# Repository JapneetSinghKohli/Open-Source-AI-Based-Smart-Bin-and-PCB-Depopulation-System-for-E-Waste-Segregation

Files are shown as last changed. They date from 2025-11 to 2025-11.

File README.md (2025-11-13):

# Open-Source-AI-Based-Smart-Bin-and-PCB-Depopulation-System-for-E-Waste-Segregation
Open-source project combining an AI-based smart bin for simple e-waste sorting with a basic PCB depopulation system. Uses computer vision to detect and classify items, separate components, and support small-scale recycling. Includes starter hardware, control code, and easy-to-use AI models.

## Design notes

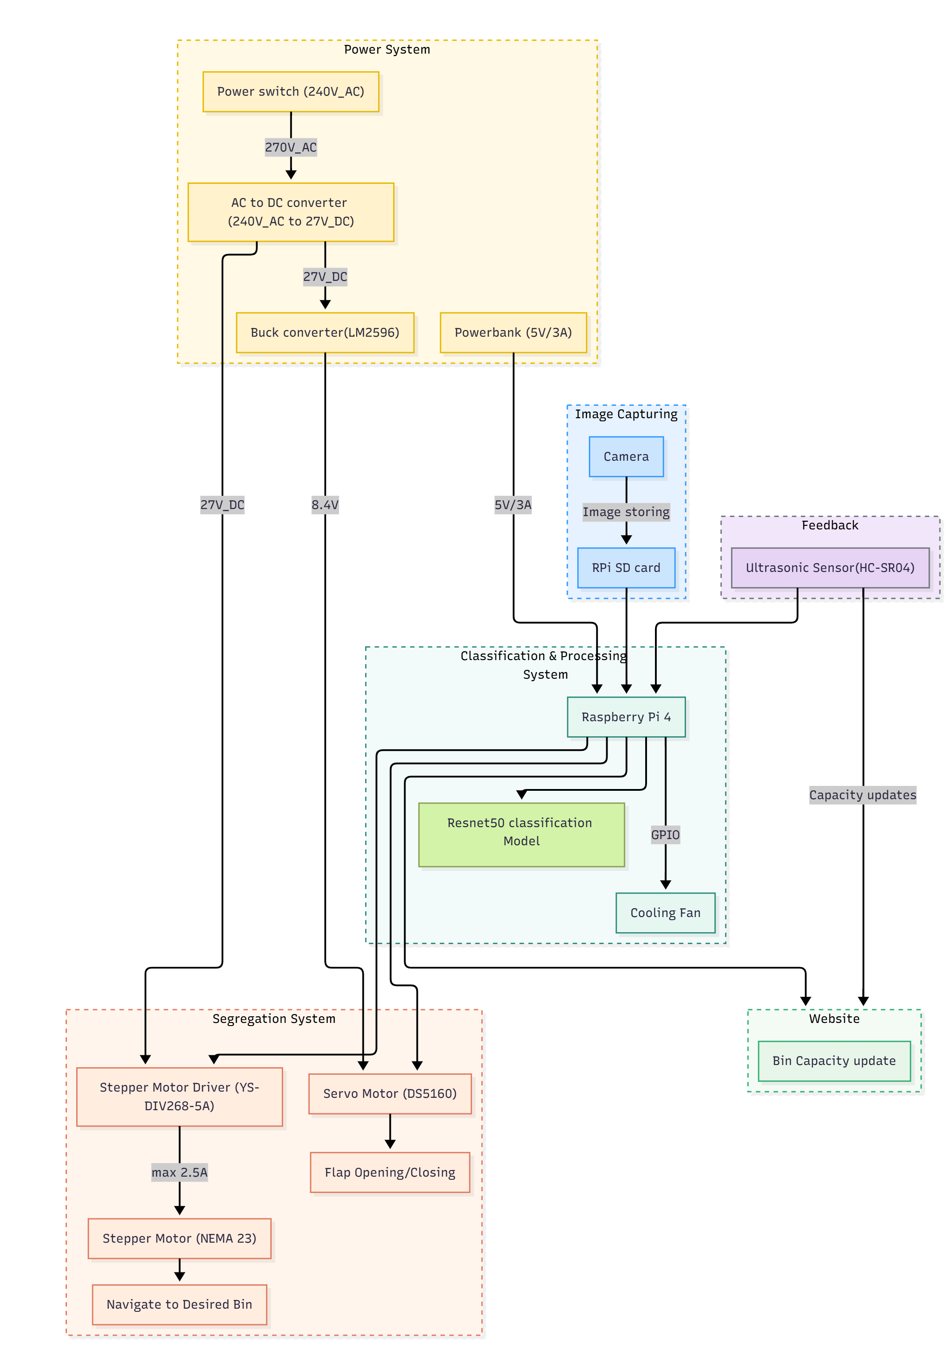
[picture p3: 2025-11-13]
Electronics design and Software/Bin-Cuircuit-Chart.png

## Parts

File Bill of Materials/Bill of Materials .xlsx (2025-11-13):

Total Spending | 48463
Part Name | Assembly Name | Type | Manufacturing Method | Assembly Method | Purchased | CAD Design Status | Reason, if CAD Not Required | Price | Quantity | Invoice Number | Bills | Date of Purchase | Vendor | Reason, if Others was choosen in any of the options
Mild Steel | Metal Frame | Raw Material for Manufacturing | Other | Welding | Offline | CAD Design Complete |  | 2196 |  | #99 | mild steel.pdf (https://drive.google.com/file/d/1QIsmK4YCOdgf_3yenXNvHcopvkcRDPWO/view?usp=sharing) | 2025-09-25 | A2Z
MS Sheet | Metal Frame | Raw Material for Manufacturing |  |  | Offline | CAD Design Complete |  | 2823 |  | #125 | MS Sheet.pdf (https://drive.google.com/file/d/1ynHdcNWmX0iU-SB3GtMpC10SeeWes1UX/view?usp=sharing) | 2025-10-08 | A2Z
Raw Material For Smart Bin | Frame | Raw Material for Manufacturing | Machining (Cutting & Drilling) | Other | Offline | CAD Design Complete |  | 3756 |  | #162 | Bill (https://drive.google.com/file/d/1nSvVK4zmFAYykZs3HyDOkAmtJ0UntyIS/view?usp=sharing) | 2025-10-14 | A2Z
Acrylic ,Paint and GI Sheet | PCB Depopulator Assembly | Raw Material for Manufacturing | Sheet Forming | Other | Offline | CAD Design Complete |  | 6469 |  | #228 | a2z bill paint acrylic and more.pdf (https://drive.google.com/file/d/1YQiOJzQaHguRpVuHmRqeH_DYfBSCvXcD/view?usp=sharing) | 2025-11-01 | A2Z
GI Sheet | Bin Structure | Raw Material for Manufacturing | Machining (Cutting & Drilling) | Other | Offline | CAD Design Complete |  | 2242 | 5 | #110 | GI sheet.pdf (https://drive.google.com/file/d/1pPkF1sUb3jVbSXK8Jkx9vuyRyn9DvjNU/view?usp=sharing) | 2025-09-30 | A2Z
MS + acrylic sheet | Covering and stand for PCB | Raw Material for Manufacturing |  |  | Offline |  |  | 9236 |  | #263 | ms+acrylic for covering .pdf (https://drive.google.com/file/d/1w8mb9un_-gyej0ABCXyPSvSI_XO86tZ7/view?usp=sharing) | 2025-11-05 | A2Z
Screws Nut Bolts | Metal Frame and Bin Structure | Fastnerm | 3D Printing | Fastening | Borrowed from DP Lab | CAD Not Required | Screws already available in Solidworks | 125 |  | #2676 | bill screw.pdf (https://drive.google.com/file/d/1irVYZd-OhjhZvoA9C_F9mrRy1DQCUNAO/view?usp=sharing) | 2025-10-10 | Ram Traders
Ultrasonic Sensor | Electrical Circuit | Purchased Finished Part | Purchased Directly | Fastening | Offline | CAD Design Complete | Electrical Component | 500 | 5 | 339/2025-26 | IMG20251017220716.heic (https://drive.google.com/file/d/1f3cun6vM0CME-H2_nhXB5eU8_ZWsTGwJ/view?usp=sharing) | 2025-10-17 | Audio Video Service Centre
WebCam | Electrical Circuit | Purchased Finished Part | Purchased Directly | Other | Online | CAD Not Required | Electrical Component | 669 | 1 | DED4-2595154 | invoice (1).pdf (https://drive.google.com/file/d/1WdGgs8KD7S56VyLepoplHJlvFNQ7aw7m/view?usp=sharing) | 2025-10-16 | Amazon
WebCam Marketplace fee |  |  |  |  |  |  |  | 5 |  | MKT-257212707 | invoice (1).pdf (https://drive.google.com/file/d/1WdGgs8KD7S56VyLepoplHJlvFNQ7aw7m/view?usp=sharing) | 2025-10-16 | Amazon
Speaker Module | Electrical Circuit | Purchased Finished Part | Purchased Directly | Other | Online | CAD Not Required | Electrical Component | 399 | 1 | ATX1-567154 | speaker bill.pdf (https://drive.google.com/file/d/1GJXc40_ItxIw6FTe9bssWk-4YPDabVqV/view?usp=sharing) | 2025-10-30 | Amazon
Speaker Module Marketplace fee |  |  |  |  |  |  |  | 5 |  | MKT-272847070 | speaker bill.pdf (https://drive.google.com/file/d/1GJXc40_ItxIw6FTe9bssWk-4YPDabVqV/view?usp=sharing) | 2025-10-30 | Amazon
Power Bank | Electrical Circuit | Purchased Finished Part | Purchased Directly | Other | Online | CAD Not Required | Electrical Component | 579 | 1 | DEL5-5873163 | invoice.pdf (https://drive.google.com/file/d/1hK2ikUXvXrY95qX3oZ5XYhJPMcIkzyN7/view?usp=sharing) | 2025-10-04 | Amazon
Power Bank Marketplace fee |  |  |  |  |  |  |  | 5 |  | MKT-224134720 | invoice.pdf (https://drive.google.com/file/d/1hK2ikUXvXrY95qX3oZ5XYhJPMcIkzyN7/view?usp=sharing) | 2025-10-04 | Amazon
Alluminium Heat Sink for Rpi4 | Electrical Circuit | Purchased Finished Part | Purchased Directly | Other | Online | CAD Not Required | Electrical Component | 638 | 1 | #3081509 | WhatsApp Image 2025-11-05 at 00.39.11_f5604e06.jpg (https://drive.google.com/file/d/1APz_-ig_qquVN-FEV0EZqeL5Ppl8Qw_G/view?usp=sharing) | 2025-10-17 | Robu
Case For Rpi4 | Electrical Circuit | Purchased Finished Part | Purchased Directly | Other | Online | CAD Not Required | Electrical Component | 201 | 1 | #3053286 | WhatsApp Image 2025-11-05 at 00.48.45_134bcea7.jpg (https://drive.google.com/file/d/199k05lIHA7o4sRsETyiCau1SaXAZe_My/view?usp=sharing) | 2025-10-04 | Robu
Vacuum Pump | Pump | Purchased Finished Part | Purchased Directly | Other | Offline | CAD Design Complete |  | 2596 | 1 | T1/00420 | vacuum bill.pdf (https://drive.google.com/file/d/1iCdUlG02D-FvGy6mnCbCQ3SVsRM7fInj/view?usp=sharing) | 2025-10-18 | Maini Electricals
Hot Plate | Heating | Purchased Finished Part | Purchased Directly | Other | Online | CAD Design Complete |  | 8024 | 1 | SST/2025-26/008 | hotplate bill.jpg (https://drive.google.com/file/d/11g4U07LEI6_g-2MESX7KZWI6NsFJYkA-/view?usp=sharing) | 2025-10-16 | Sishma Scientific Traders
Fan Blower |  |  |  |  | Online |  |  | 2006 | 1 | 589 | Fan Blower Bill.jpg (https://drive.google.com/file/d/1GNX6yTsFkwgpAt6QHHy39YnqiH1XPK6k/view?usp=sharing) | 2025-10-24 | Mankoo Electric Works
Ceramic Insulation Blanket |  | Purchased Finished Part | Purchased Directly |  | Online | CAD Design Complete |  | 1992 | 1 | IN-568 | Ceramic Blanket.pdf (https://drive.google.com/file/d/103j5b9NfD07mp-TA_c69nZBMUl-d2isc/view?usp=sharing) | 2025-10-28 | Amazon
Ceramic Insulation Blanket Marketplace fee |  |  |  |  |  |  |  | 5 |  | MKT-269632534 | Ceramic Blanket.pdf (https://drive.google.com/file/d/103j5b9NfD07mp-TA_c69nZBMUl-d2isc/view?usp=sharing) | 2025-10-28 | Amazon
Extention Board |  | Raw Material for Manufacturing | Other | Other | Offline | CAD Not Required |  | 1060 | 1 | 3835 | Extension Board Bill.jpg (https://drive.google.com/file/d/1-SyfV-J8QsLSe0toX0ElAZfBRrLgyiDw/view?usp=sharing) | 2025-10-25 | Jiwan Electric Stores
Motor Driver DRV8825 |  | Purchased Finished Part | Purchased Directly |  | Offline |  | Electrical Component | 120 | 1 | 338/2025-26 | IMG20251017220633.heic (https://drive.google.com/file/d/1wcqMyeiRGANEz7x_3AZ8HlOxYGn_FrIG/view?usp=sharing) | 2025-10-17 | Audio Video Service Centre
Load Cell + HX711 |  | Purchased Finished Part | Purchased Directly |  | Offline |  | Electrical Component | 240 | 1+1 | 340/2025-26 | IMG20251017220651.heic (https://drive.google.com/file/d/1sXZ2I21_zPG8-pErcfny125J8XbTL-0H/view?usp=sharing) | 2025-10-17 | Audio Video Service Centre
YS-DIV268-5A Stepper Motor Driver | Electrical Circuit | Purchased Finished Part | Purchased Directly |  | Online |  |  | 1359 | 1 | DEL5-3833545 | motor driver for stepper.pdf (https://drive.google.com/file/d/1ZaReP2N4-LilRE3OmvAkqA1qvz2RBtmh/view?usp=sharing) | 2025-11-01 | Amazon
YS-DIV268-5A Stepper Motor Driver Marketplace fee |  |  |  |  |  |  |  | 5 |  | MKT-276489144 | motor driver for stepper.pdf (https://drive.google.com/file/d/1ZaReP2N4-LilRE3OmvAkqA1qvz2RBtmh/view?usp=sharing) | 2025-11-01 | Amazon
Lab Gloves | Safety | Purchased Finished Part | Purchased Directly |  | Online | CAD Not Required | Safety Component | 399 | 1 | ATX1-723 | gloves.pdf (https://drive.google.com/file/d/1EiizKb7cILWFiQO9119dt_ykNaHlOZkI/view?usp=sharing) | 2025-10-30 | Amazon
Lab Gloves Marketplace fee |  |  |  |  |  |  |  | 5 |  | MKT-273642335 | gloves.pdf (https://drive.google.com/file/d/1EiizKb7cILWFiQO9119dt_ykNaHlOZkI/view?usp=sharing) | 2025-10-30 | Amazon
Power supply | Electrical Circuit | Purchased Finished Part | Purchased Directly |  | Online |  |  | 799 | 1 | RNLH-6357 | power supply bill.pdf (https://drive.google.com/file/d/15PSYE9HjfH0hNEDoG0ndsTIOTZ4xvLA6/view?usp=sharing) | 2025-11-03 | Amazon
Power supply Marketplace fee |  |  |  |  |  |  |  | 5 |  | MKT-280663344 | power supply bill.pdf (https://drive.google.com/file/d/15PSYE9HjfH0hNEDoG0ndsTIOTZ4xvLA6/view?usp=sharing) | 2025-11-03 | Amazon
Battery | Electrical Circuit | Purchased Finished Part | Purchased Directly | Other | Borrowed from DP Lab | CAD Design Complete | Electrical Component | 0 | 1
Servo | Electrical Circuit | Purchased Finished Part | Purchased Directly | Other | Borrowed from DP Lab | CAD Design Complete | Electrical Component | 0 | 2
Stepper Motor | Electrical Circuit | Purchased Finished Part | Purchased Directly | Other | Borrowed from DP Lab | CAD Design Complete |  | 0 | 1
Raspberry Pi | Electrical Circuit | Purchased Finished Part | Purchased Directly | Other | Borrowed from DP Lab | CAD Design Complete | Electrical Component | 0 | 1
Micro Sd card | Electrical Circuit | Purchased Finished Part | Purchased Directly | Other | Borrowed from DP Lab | CAD Design Complete | Electrical Component | 0 | 1
TOTAL |  |  |  |  |  |  |  | 48463

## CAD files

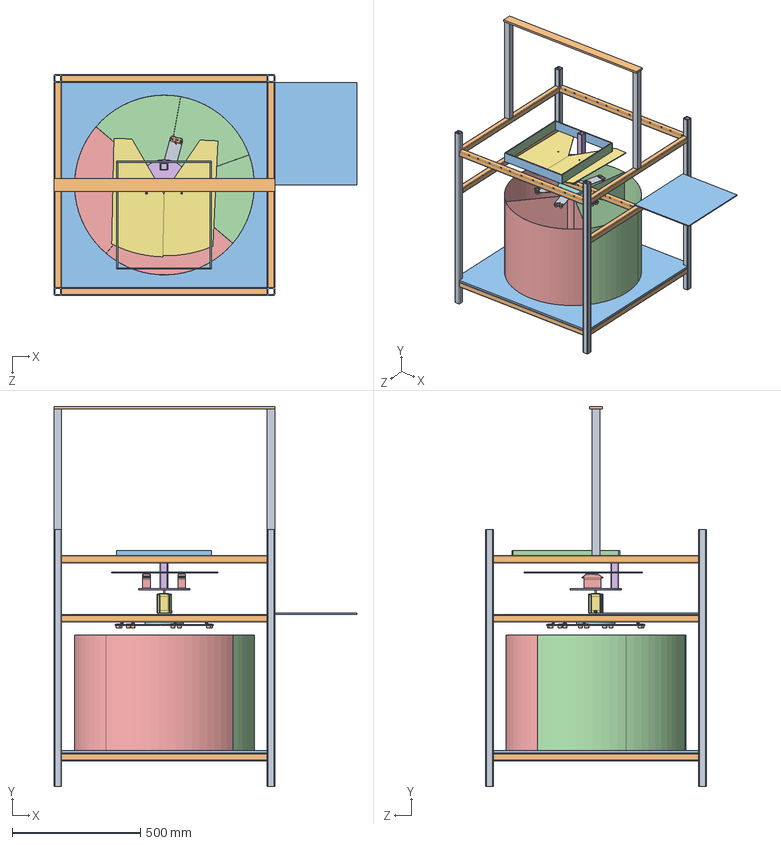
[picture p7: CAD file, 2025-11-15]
CAD/AI Based Smart Bin/Assem1.SLDASM
1180.0 x 1480.0 x 860.0 mm
Bar_2 x 4
bar x 13
sheet
Bin_Compart x 3
Disc
Stepper motor NEMA 23HS7430
mount
bAR1 x 2
camera mount
Wall_1 x 2
wall_2 x 2
ft6560m 60kg.cm.step x 2
wall holder
flaps x 2
UltraHolder
HC-SR04 Ultrasonic Sensor Holder x 5
HCSR04 Ultrasonic Sensor x 5
electronic holder

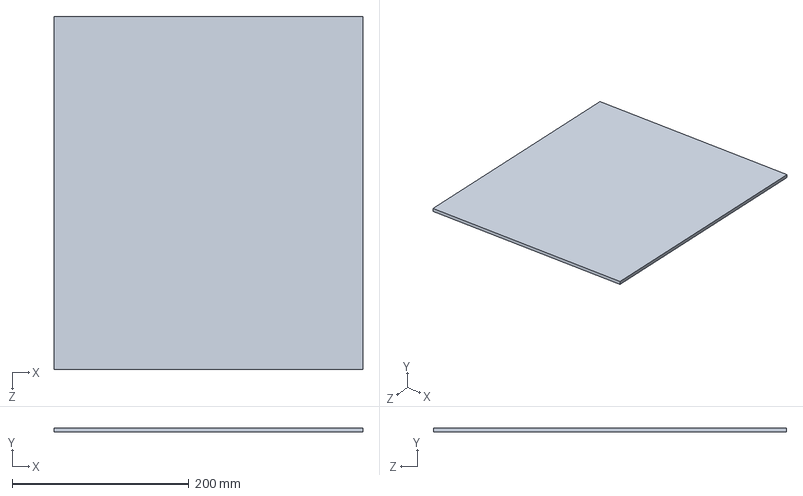
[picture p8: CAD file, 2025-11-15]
CAD/AI Based Smart Bin/electronic holder.SLDPRT
350.0 x 5.00 x 400.0 mm

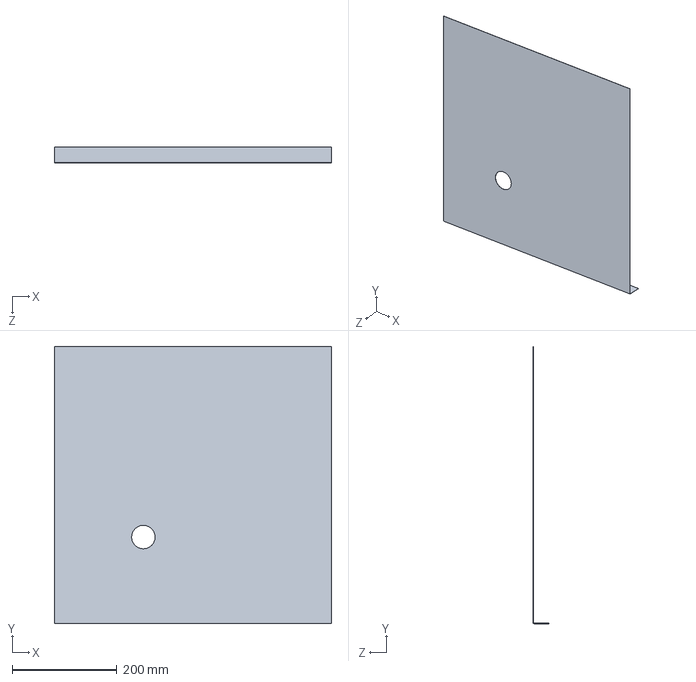
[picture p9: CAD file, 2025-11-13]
CAD/PCB Depopulator/right.SLDPRT
530.0 x 530.0 x 30.4 mm

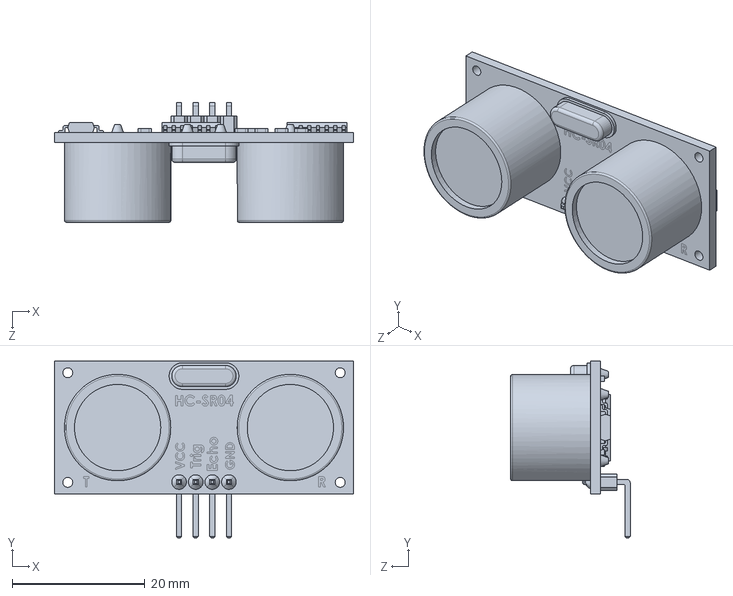
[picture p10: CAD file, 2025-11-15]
CAD/AI Based Smart Bin/HCSR04 Ultrasonic Sensor.SLDPRT
45.0 x 26.6 x 18.0 mm

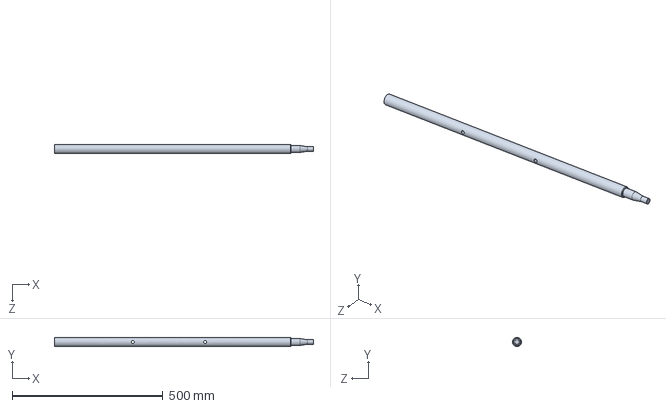
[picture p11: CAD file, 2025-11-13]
CAD/PCB Depopulator/Cylinder.SLDPRT
860.0 x 30.0 x 30.0 mm

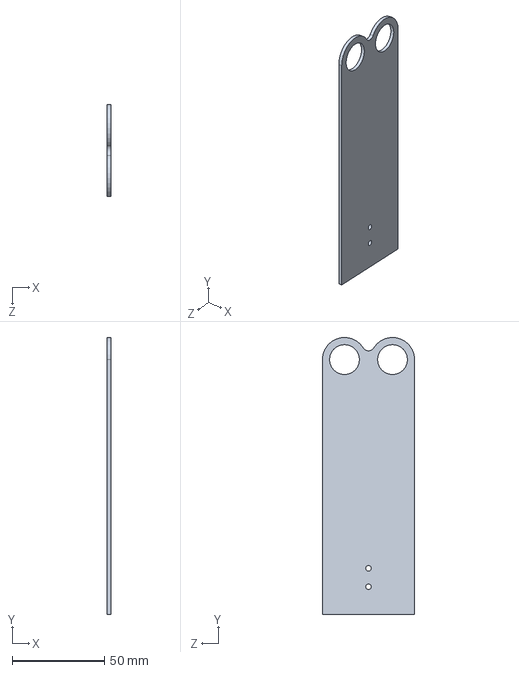
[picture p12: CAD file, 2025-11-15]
CAD/AI Based Smart Bin/HC-SR04 Ultrasonic Sensor Holder.SLDPRT
2.00 x 150.0 x 50.0 mm

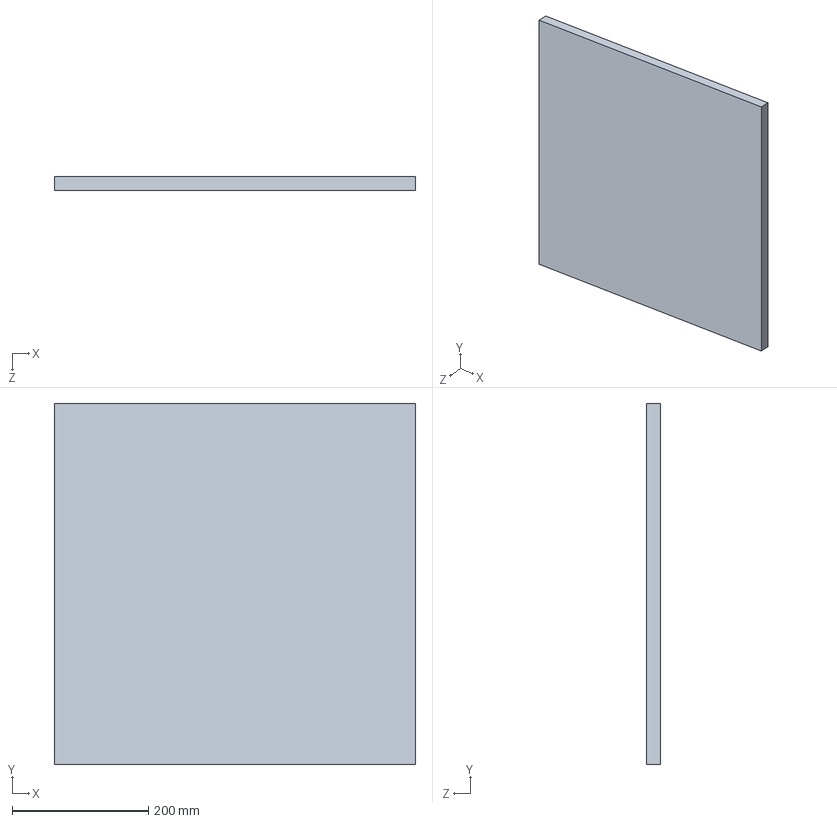
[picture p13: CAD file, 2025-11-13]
CAD/PCB Depopulator/FRONT.SLDPRT
530.0 x 530.0 x 20.0 mm

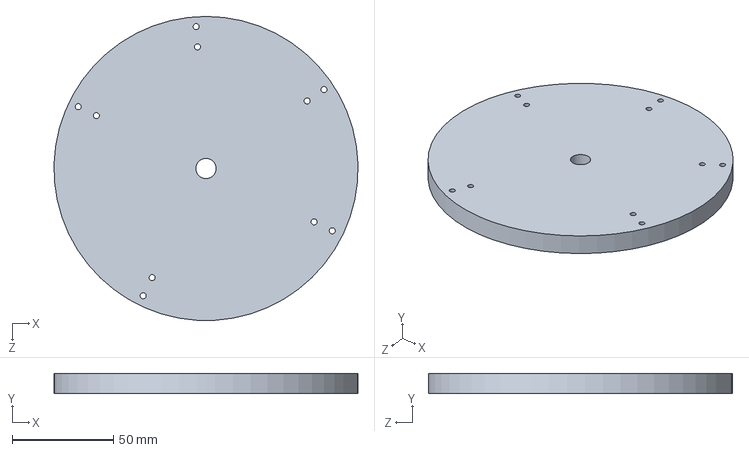
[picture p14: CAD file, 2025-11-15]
CAD/AI Based Smart Bin/UltraHolder.SLDPRT
149.9 x 10.0 x 150.0 mm

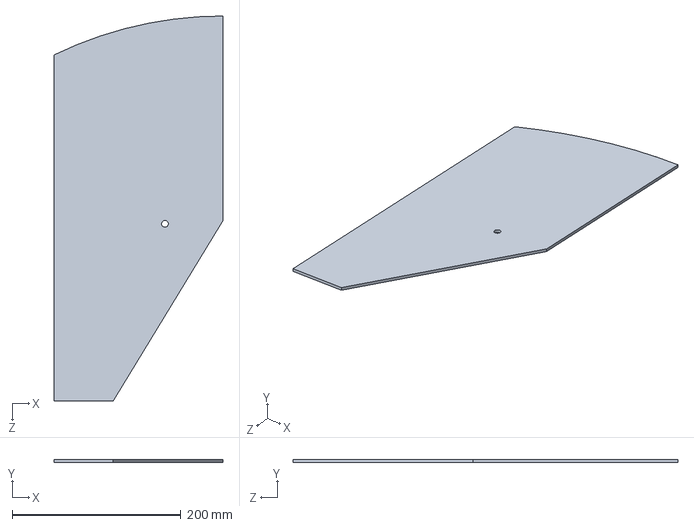
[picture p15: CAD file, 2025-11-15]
CAD/AI Based Smart Bin/flaps.SLDPRT
200.0 x 3.50 x 456.8 mm

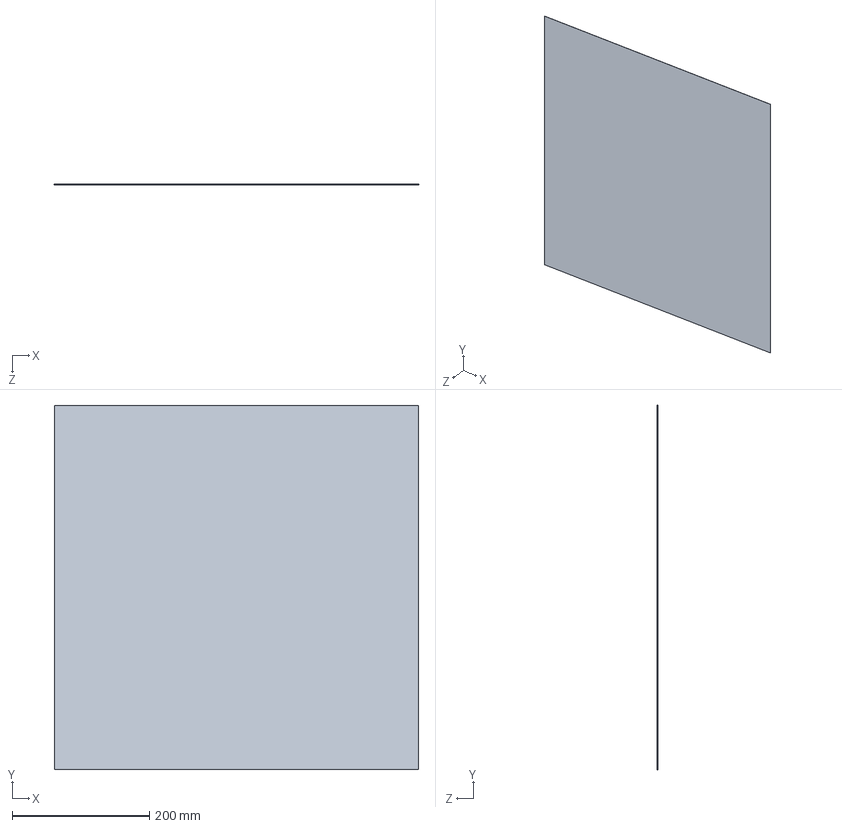
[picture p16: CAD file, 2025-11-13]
CAD/PCB Depopulator/back.SLDPRT
530.0 x 530.0 x 0.35 mm

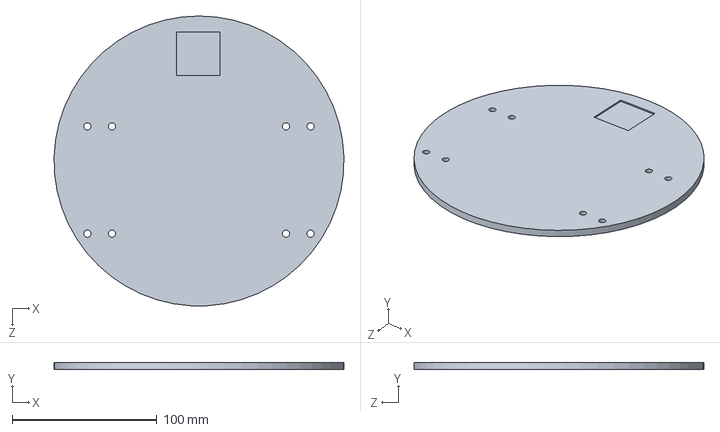
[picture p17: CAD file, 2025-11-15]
CAD/AI Based Smart Bin/Disc.SLDPRT
199.9 x 5.00 x 200.0 mm

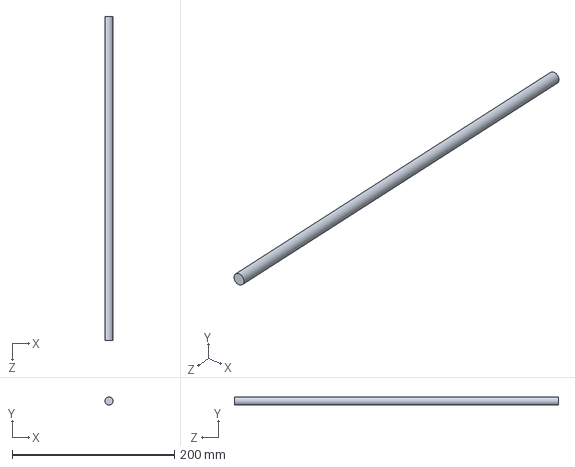
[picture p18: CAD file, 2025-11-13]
CAD/PCB Depopulator/Holder.SLDPRT
10.0 x 10.0 x 400.0 mm

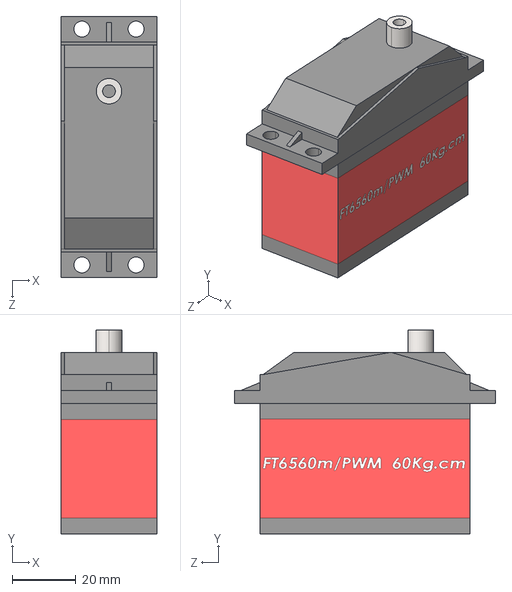
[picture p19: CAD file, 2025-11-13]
CAD/AI Based Smart Bin/ft6560m 60kg.cm.STEP
30.0 x 64.0 x 82.0 mm

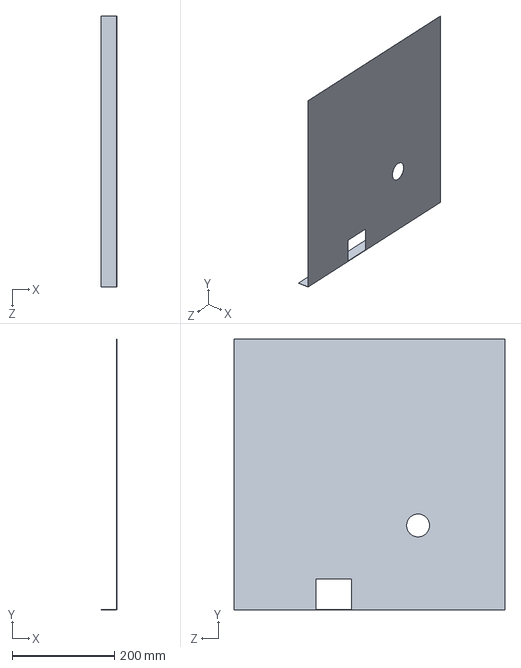
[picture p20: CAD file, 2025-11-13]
CAD/PCB Depopulator/LEFT.SLDPRT
30.4 x 530.0 x 530.0 mm

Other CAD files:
CAD/PCB Depopulator/hinge.SLDASM
CAD/PCB Depopulator/TOP.SLDPRT
CAD/AI Based Smart Bin/mount.SLDPRT
CAD/PCB Depopulator/second layer.SLDPRT
CAD/AI Based Smart Bin/Bar_2.SLDPRT
CAD/AI Based Smart Bin/Bin_Compart.SLDPRT
CAD/AI Based Smart Bin/Part2.SLDPRT
CAD/AI Based Smart Bin/Stepper motor NEMA 23HS7430.SLDPRT
CAD/AI Based Smart Bin/Wall_1.SLDPRT
CAD/AI Based Smart Bin/bAR1.SLDPRT
CAD/AI Based Smart Bin/bar.SLDPRT
CAD/AI Based Smart Bin/camera mount.SLDPRT
CAD/AI Based Smart Bin/sheet.SLDPRT
CAD/AI Based Smart Bin/wall holder.SLDPRT
CAD/AI Based Smart Bin/wall_2.SLDPRT
CAD/PCB Depopulator/Bottom.SLDPRT
CAD/PCB Depopulator/ceramic.SLDPRT
CAD/PCB Depopulator/hing1.SLDPRT
CAD/PCB Depopulator/hinge2.SLDPRT
CAD/PCB Depopulator/hinge3.SLDPRT

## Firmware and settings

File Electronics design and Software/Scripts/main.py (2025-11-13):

# scripts/main.py
from pathlib import Path
from gpiozero import Device
from gpiozero.pins.pigpio import PiGPIOFactory
import time

from classify_image import classify_image
from capture_image import capture  # <-- added this import



'''Add catagory to stepper '''


# This sets the *default* factory for all gpiozero devices
Device.pin_factory = PiGPIOFactory()



import new_stepper_code #importing whole module to ensure gpio initialization
import servo_control  #importing whole module to ensure gpio initialization


CATEGORY_MAP = {
    "Smartwatch": 1, "Mobile": 1,
    "Headphones": 2, "Mouse": 1, "Remote Control": 2,
    "Keyboard": 5, "Printer": 5,
    "Battery": 3, "PCBs": 4,
}


def main():
    a_time=time.time()
    print("Capturing image...")
    image_path = capture()  # capture and get file path

    print("Running classification...")
    label = classify_image(str(image_path))

    print(f"\n✅ Final Prediction: {label}\n")

 
    category_number = CATEGORY_MAP.get(label)
    print(f"Waste falls in Category: {category_number}")

    # Motor Control 
    new_stepper_code.move_to_category(category_number)
    time.sleep(3)  # Wait a moment at the category position
    servo_control.run_servo()
    time.sleep(3)  # Wait a moment before returning
    new_stepper_code.return_to_initial(category_number)
    time.sleep(1)




    # Finally, close the factory
    Device.pin_factory.close()
    print("Shared pigpio factory closed.")
    b_time=time.time()
    print(f"Total runtime:{b_time-a_time}")
if __name__ == "__main__":
    main()

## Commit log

2025-11-13 bill of materials added
    [Bill of Materials .xlsx]
2025-11-13 CAD files updated
    [Assem1.SLDASM, Assem2.SLDASM, Bottom.SLDPRT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]
